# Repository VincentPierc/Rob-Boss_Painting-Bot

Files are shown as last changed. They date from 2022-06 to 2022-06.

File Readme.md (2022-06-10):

# Rob Boss - Painting Robot (Disciple of Bob Ross)
#### Contributors: Vincent Pierce, Conrad Kinsey, Hayden Jeanor

## Contents

- [Overveiw](https://github.com/VincentPierc/Rob-Boss_Painting-Bot#overview)
- [Mechanical Design](https://github.com/VincentPierc/Rob-Boss_Painting-Bot#mechanical-design)
    - [Design Process](https://github.com/VincentPierc/Rob-Boss_Painting-Bot#design-process)
        - [First Iteration](https://github.com/VincentPierc/Rob-Boss_Painting-Bot#first-iteration)
        - [Redesign](https://github.com/VincentPierc/Rob-Boss_Painting-Bot#redesign)
    - [Final Implementation](https://github.com/VincentPierc/Rob-Boss_Painting-Bot#final-implementation)
        - [Paintbrush Actuation](https://github.com/VincentPierc/Rob-Boss_Painting-Bot#paintbrush-actuation)
        - [Matching the 2D Kinematics](https://github.com/VincentPierc/Rob-Boss_Painting-Bot#matching-the-2d-kinematics)
        - [Main Housing](https://github.com/VincentPierc/Rob-Boss_Painting-Bot#main-housing)
    - [Key Takeaways](https://github.com/VincentPierc/Rob-Boss_Painting-Bot#key-takeaways)
        - [Gear Reduction](https://github.com/VincentPierc/Rob-Boss_Painting-Bot#gear-reduction)
        - [Don’t Reinvent the Wheel](https://github.com/VincentPierc/Rob-Boss_Painting-Bot#dont-reinvent-the-wheel)
        - [Add a Third Dimension](https://github.com/VincentPierc/Rob-Boss_Painting-Bot#add-a-third-dimension)
- [Electrical Design](https://github.com/VincentPierc/Rob-Boss_Painting-Bot#electrical-design)
    - [Motor Controlling](https://github.com/VincentPierc/Rob-Boss_Painting-Bot#motor-controlling)
    - [Solenoid Actuating](https://github.com/VincentPierc/Rob-Boss_Painting-Bot#solenoid-actuating)
- [Software Design](https://github.com/VincentPierc/Rob-Boss_Painting-Bot#software-architecture)
    - [Software Architecture](https://github.com/VincentPierc/Rob-Boss_Painting-Bot#software-architecture)
        - [Draw Wrapper](https://github.com/VincentPierc/Rob-Boss_Painting-Bot#draw-wrapper)
        - [Find Thetas](https://github.com/VincentPierc/Rob-Boss_Painting-Bot#find-thetas)
     - [Computer Code](https://github.com/VincentPierc/Rob-Boss_Painting-Bot#computer-code)
        - [Live Plotting](https://github.com/VincentPierc/Rob-Boss_Painting-Bot#live-plotting)
        - [Gif Generation](https://github.com/VincentPierc/Rob-Boss_Painting-Bot#gif-generation)
        - [Theta Timeline](https://github.com/VincentPierc/Rob-Boss_Painting-Bot#theta-timeline)
    - [Kinematics](https://github.com/VincentPierc/Rob-Boss_Painting-Bot#kinematics)
        - [Newton Raphson](https://github.com/VincentPierc/Rob-Boss_Painting-Bot#newton-raphson)

## Overview
Rob Boss (disciple of Bob Ross) is a 2 1/2 degree of freedom pen-plotting robot with a twist. This robot is capable of painting whatever HPGL file that is uploaded to its hard-drive. The project was created for our ME 405 Mechatronics term project at California Polytechnic State University San Luis Obispo.

With an STM32 Arm Cortex MCU on a Nucleo-64 board as the brains of the robot, we designed a surrounding electro-mechanical system from scratch to give a 3-dimensional structure to the robot. In combination with the software we designed and uploaded on the STM32, the robot arm can paint any image you can draw on illustrating software. Detailed design parameters can be found in the [Mechanical Design](https://github.com/VincentPierc/Rob-Boss_Painting-Bot#mechanical-design), [Software Design](https://github.com/VincentPierc/Rob-Boss_Painting-Bot#software-design), and [Electrical Design](https://github.com/VincentPierc/Rob-Boss_Painting-Bot#electrical-design) sections.

The completed robot is able to synchronously draw any HPGL image with color, refill when low on paint, and plot the image on a computer. The video below shows Rob Boss’s full capabilities.

Rob Boss - Painting Robot (https://www.youtube.com/watch?v=zsSy63GS3jI)

## Mechanical Design

### Design Process

Considering all group members of the project are electrical engineers, we decided to go with a rather basic mechanical design which ended up being rather complex after multiple iterations. The mechanical design of the robot was largely based upon two parameters:

1. adhere to the [kinematics](https://github.com/VincentPierc/Rob-Boss_Painting-Bot#kinematics) of the program we were implementing
	- this required lighter components to be used towards the end of the arm because of the large amount of leverage being produced by the arm being in air
2. design around the materials we had at our disposal or that we could buy on a college student's budget

#### First Iteration
 Because our design was based on the traditional "arm" configuration with a "shoulder" and "elbow" joint, we would need a stepper motor driving each joint. In the first iteration of the robot, we chose to use one large stepper motor to drive the shoulder joint and one smaller stepper motor to drive the elbow joint. This iteration had the placement of the smaller motor at the location of the elbow joint, so it required the motor to be lighter. This ended up presenting torque problems in the future.

 In order to transfer the motor torque into arm angle movement, simple elbow pieces were created to directly transfer the movement to the arm. The two armatures, main housing, and the motor elbows were designed in solidworks and 3D printed. The first iteration, shown below, failed because the small motor did not produce enough torque to move the small arm.

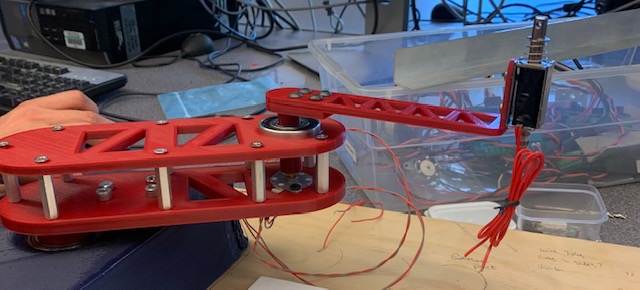
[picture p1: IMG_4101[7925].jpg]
First Iteration


#### Redesign
Upon the realization that we could not use the small motor, we redesigned the large arm to use a large motor to drive the small arm mounted above the large motor already driving the large arm. Placing the small arm motor at the shoulder joint reduced the weight towards the end of the arms. However, it required the use of a driving belt and parametric pullies.

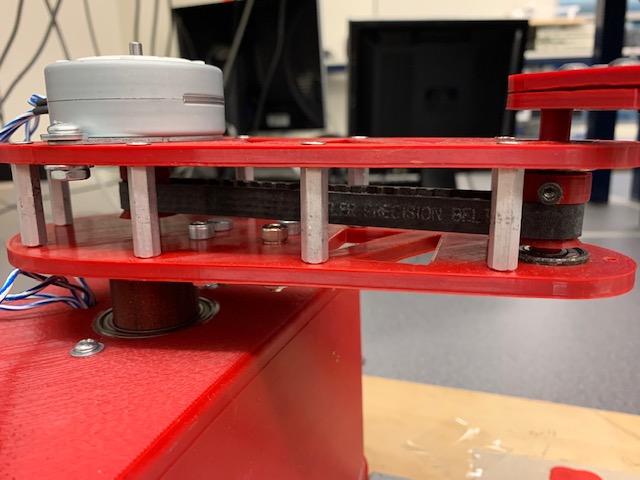
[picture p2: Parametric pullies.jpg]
Parametric Pulley System


Through the guidance of our fellow classmates who are majoring in mechanical engineering, we did not have to design our own parametric pullies. Rather, we pulled [customizable parametric pullies](https://www.thingiverse.com/thing:16627) from [Thingiverse](https://www.thingiverse.com/) and edited them on [OpenSCAD](https://openscad.org/) to meet our mechanical design needs. In order to have variable tensioning of the drive belt, the holes that mount the small arm motor are elongated.

### Final Implementation
The images below show the final form of the robot. Many of the parts of the robot were designed to be fastened together using hardware that was found in the lab. Each of the [parts](https://github.com/VincentPierc/Rob-Boss_Painting-Bot/tree/main/Rob_Boss_Mechanical_Design) were 3D printed and assembled using the fasteners. Another standout design aspect is the reduction of weight in the armatures while maintaining rigidity using triangular cutouts.

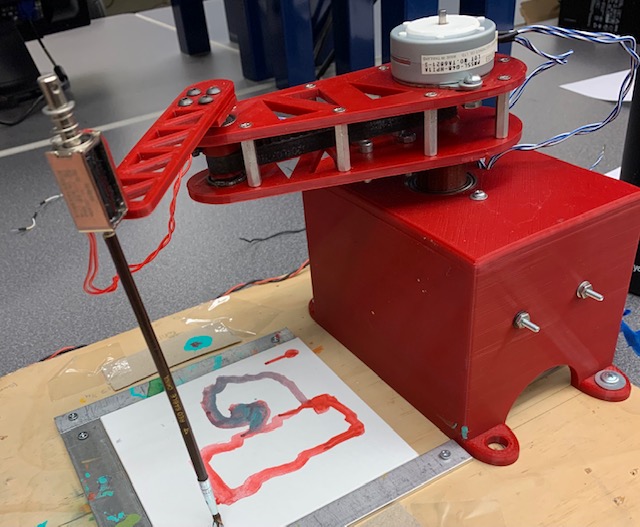
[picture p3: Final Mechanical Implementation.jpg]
Final Mechanical Implementation


#### Paintbrush Actuation
For the half degree of freedom, we chose a lightweight [solenoid actuator](https://www.amazon.com/dp/B07VC5JKYG?psc=1&ref=ppx_yo2ov_dt_b_product_details). This solenoid provides 5N of push/pull force which is plenty to raise and lower a 50 gram paintbrush. The modified paint brush being actuated was threaded into the end of the solenoid plunger.

#### Matching the 2D Kinematics
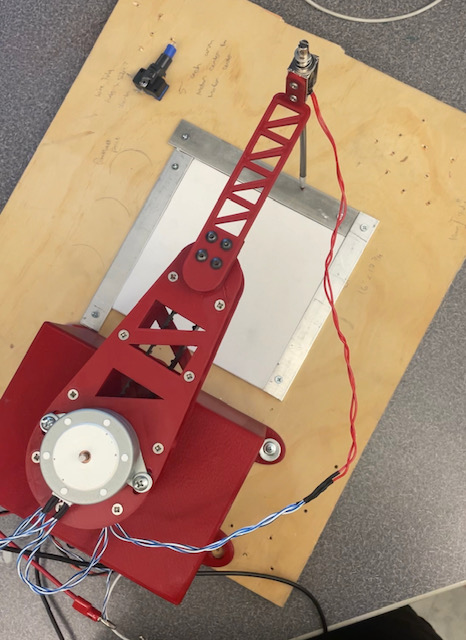
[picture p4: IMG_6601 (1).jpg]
Armature View


Top down view of robot arm used for drawing. Mechanical design implemented a theta-theta rotation about 2 pivot points which, when combined with a solenoid, produced 2 1/2 degrees of freedom. To satisfy the calculated kinematics, both arms were designed so that they would have equivalent lengths from pivot point to pivot point and from pivot point to the center of the paint brush. These lengths were chosen to be 5 inches each because a 10 inch radius covers the desired painting area.

#### Main Housing
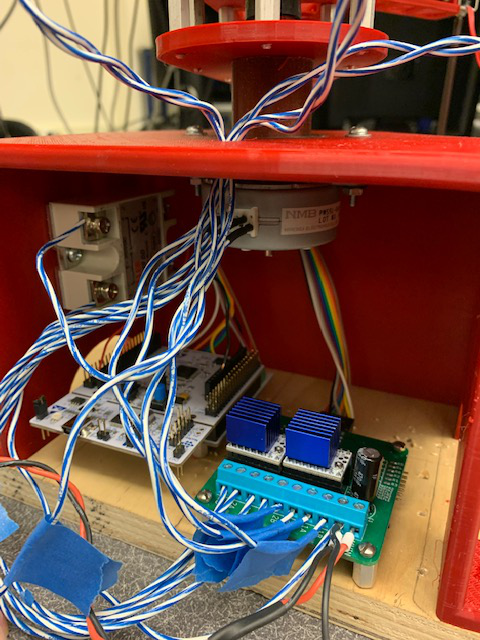
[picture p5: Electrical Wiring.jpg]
Housing View


Side View of robot main housing. The housing was designed so that the arm is ~ 5 inches off canvas it will draw on. Additionally, all electronics (solenoid relay, STM32, Shoe of Brian and breakout board) including their wiring could be securely placed out of reach from the rotating arm.

### Key Takeaways

#### Gear Reduction
Gear reduction from the motor would increase the resolution. The large arm motor ended up having much worse resolution even with microstepping implemented. In hindsight, having the motor drive the arm using another parametric pulley system with gear reduction would have resulted in slower painting speed but much better resolution.

#### Don't Reinvent the Wheel
Starting the project, we originally thought that every aspect of the project had to be original and designed ourselves. In reality, trying to design gears in solidworks is an unnecessary waste of time when someone else on the internet has already done so and published their work for free. Rather, our time is more well spent designing our own innovations.

#### Add a Third Dimension
Originally, both arms were going to be designed using only one dimension. However, the larger arm ended up getting a top which allowed for more stability in the small arm elbow piece that now had two contact points with barings rather than one. The small arm as well as the large arm motor elbow ended up not being so rigid because of the lack of a "3rd dimension."

## Electrical Design
The three actuating devices (motors and solenoid) of the robot are controlled via an electrical system consisting of a central microcontroller, motor-interfacing breakout board, and power system. The overall wiring between the devices are shown below.

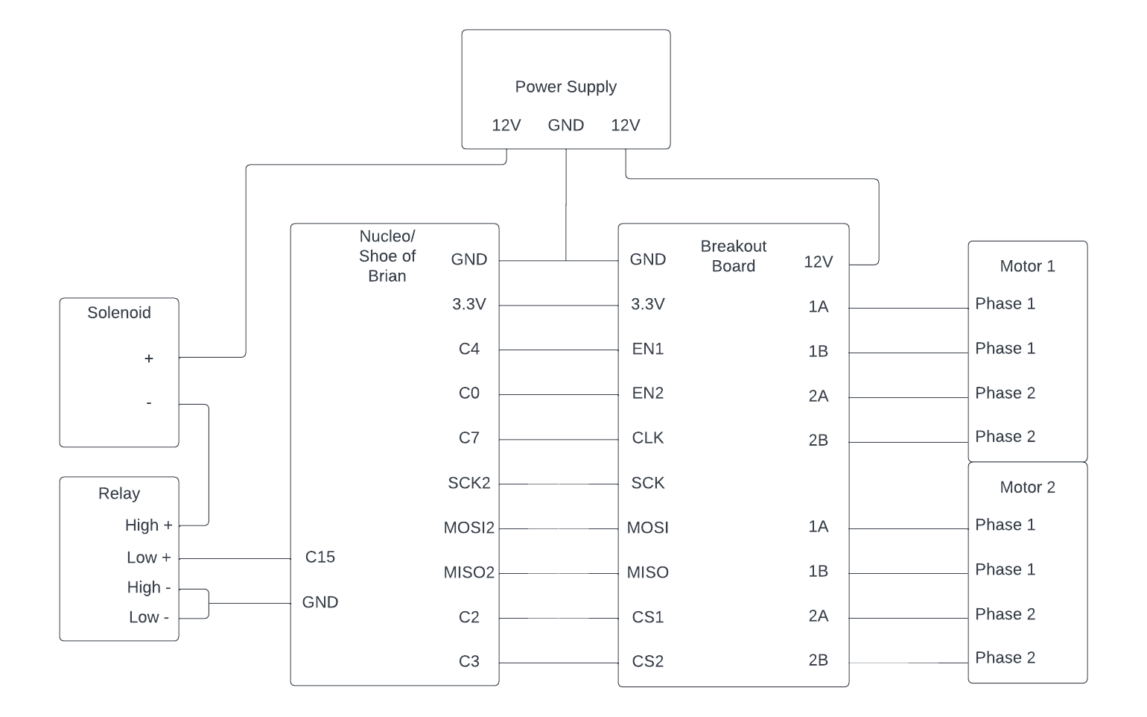
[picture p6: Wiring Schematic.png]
Wiring Diagram


### Motor Controlling
The motors are being controlled by the microcontroller sending position signals via SPI over the bus connected between the MCU and the motor-interfacing breakout board. The breakout board houses a [TMC2208](https://www.mouser.com/datasheet/2/256/TMC220x_TMC2224_datasheet_Rev1_09-1879275.pdf) stepper motor driver and [TMC4210](https://www.mouser.com/datasheet/2/256/TMC4210_Datasheet_Rev_1_05-1878621.pdf) microcontroller-motordriver interface for each motor. To simplify the complexity of these chips, they convert motor position to SPI signals readable by the MCU and vice versa to get real time motor position and send target motor position.

### Solenoid Actuating
 In order to provide the power needed for the solenoid to acutate, a [solid state relay](https://www.amazon.com/SSR-100DD-Solid-State-Relay-Module/dp/B07PFDJQLV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) was used to convert a 3.3V signal from the microcontroller to 12V, 600mA power supply signal.

## Software Design

### Software Architecture
The overarching software architecture uses a cooperative multitasking scheduler. Each of the tasks the robot performs was created with the other tasks in consideration. The robot first parses through the file and creates a list with the first element of which being the instruction name and all subsequent elements being the numbers associated with that instruction. The file then runs through the two processing tasks to interpret the instructions, move the robot, and send the data to the computer.

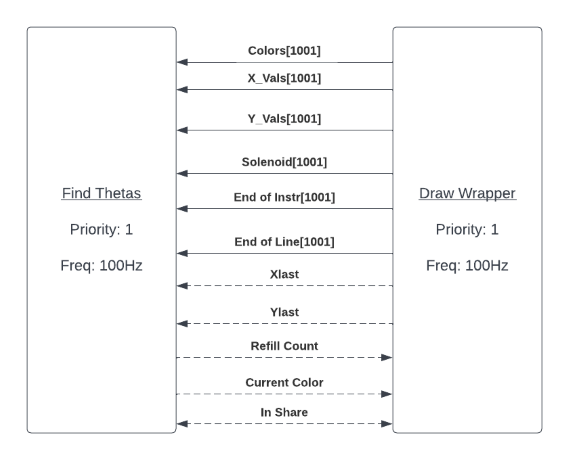
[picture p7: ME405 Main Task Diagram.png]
Main Task Diagram


#### Draw Wrapper
The main task of the assignment is the Draw Wrapper task. The function is named Draw Wrapper because it calls the draw function. The actual purpose of the task is to iterate through the instruction list and process a single instruction each time it is called. It does so through popping the first value of the instruction list then calling the draw function on the popped instruction list. It is inside of the draw function that the instruction is processed. If the instruction is an IN instruction, the function will place the initial point of (0,0) into the X_Vals and Y_Vals queues to set the initial location of the motor when it runs. If an IN instruction is called after this, it will be deemed the end of the list and the motors will reset to their fully extended position. If the instruction is SP, the color selected by the SP instruction will be set as the value for the shared variable curcolor. If a PD or PU function is received, the function will first set the pen value to 1 or 0 with 1 being the pen down state and 0 being the pen up state. The function then runs the interpolation function created in Lab 3. All x and y values are then pushed into the X_Vals and Y_Vals queues. When these values are pushed into the queues, the values of the current color, whether this is the end of instruction and whether this is the end of the file, are also pushed to their respective queues. This task runs with a period of 10ms.

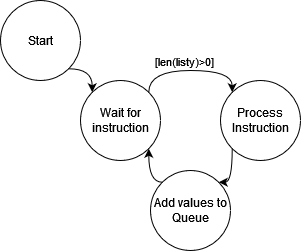
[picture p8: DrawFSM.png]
drawFSM


#### Find Thetas
When the task is first initialized it generates a list of size 2 that will be used for temporary theta storage. To be more memory efficient, this could have been a float array of size 2. However, the difference between an array of size 2 and a list of size 2 was deemed negligible in this case since the list would be reused in each call. After creating the list, the remaining variables represent the initial guesses for the Newton Raphson function and an initial color value of curcolor. The function then checks the size of the X_Vals queue to see if the Draw Wrapper task has been called. If there are values in the queue, they are read and fed into the Newton Raphson function to find the theta values. Once appropriate data values are found, they are converted to between pi and -pi. This is to prevent the robot from spinning in circles after finding a solution a full rotation off from the robot's current position. The theta, solenoid, EOI(End Of Instruction), and EOF (End Of File) bits are then sent over UART to the computer for the live drawing. Once that is done, the motors are then moved to the new theta positions.

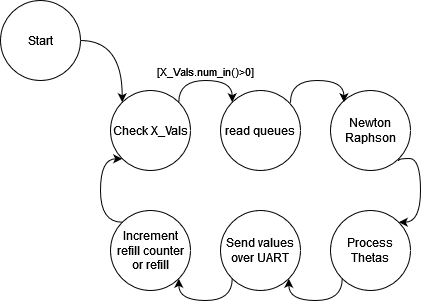
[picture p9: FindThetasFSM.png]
thetaFSM


### Computer Code
For the "Bells and Whistles" of our assignment, we opted to go with a computer software implementation. The code, running simultaneously to the code on the Nucleo, generates various graphs to visualize what Rob is supposed to be doing. As the computer code is all one function named main(), we have split up the portions by generated graphic for ease of reading.

[Code can be found here](https://github.com/VincentPierc/Rob-Boss_Painting-Bot/blob/main/Code/Computer_Code.py)

#### Live Plotting
The live plotting is the first part of the computer code to be run after initializing all necessary variables. The function makes use of a double nested while loop. The first loop waits for the EOF bit and sets the input list to be zeros, while the second waits for the EOI bit and sets the list to the incoming values. Each time these values are read from the UART, a graph is generated with all past points and the current point. The graph also has an updated location of the lines representing the robot's arms, with these arms pointing to the latest point. Lines are only drawn between points in the case of both solenoid bits being set high and are drawn using the color input over UART.

#### Gif Generation
The Gif Generation function runs directly after the Live plotting finishes and mirrors the Live Plotting portion closely. The difference is that it uses a list of the UART and a counter to iterate instead of the two for loops present in the Live Plotting function. The output of this section is an animated gif saved under the name "func.gif".

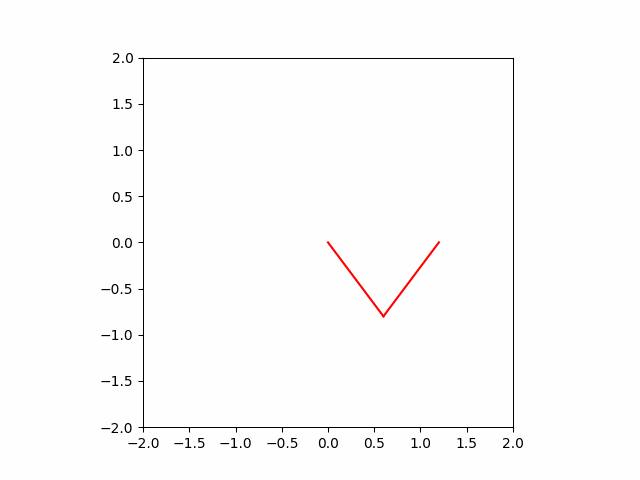
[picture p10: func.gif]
Example


#### Theta Timeline
Once the gif of the plot is generated, a graph showing the values of theta 1 and 2 over the number of UART reads is generated. The graph served to confirm our robot was generating proper values during the testing stages. We left the graphs in as they serve as reassurance that the robot is functioning properly and are a clear indicator the computer code has finished running.

### Kinematics
The requirement of the project is to create a robot that draws with two and a half degrees of freedom not using the traditional cartesian coordinate system. For this project, we implemented a design that has two finite length armatures with variable angles of direction.

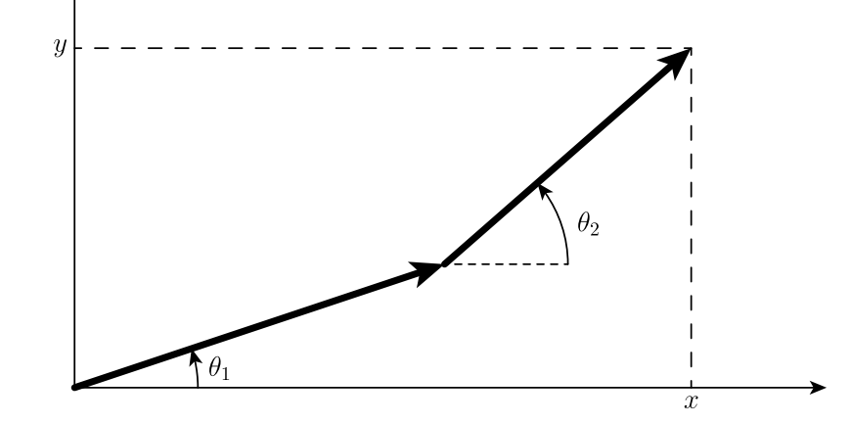
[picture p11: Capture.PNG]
Forward Kinematics


#### Newton Raphson
Even though the robot works in terms of two angles, all the data parsed from the input (HPGL) file is in terms of cartesian coordinates. The heart of Rob's ability to draw lies in the Newton Raphson algorithm which allows us to convert (x, y) coordinates into (theta1, theta2) coordinates. Allowing the robot to draw images like the flower drawn below.

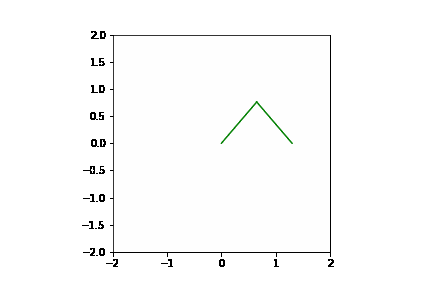
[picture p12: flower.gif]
Animation Drawing


This conversion, or mapping, of coordinate systems is considered kinematics and deals with how driving actuators (motors) affects end-effector coordinates (pen-plotter position). Newton Raphson allows us to iteratively solve for motor coordinates which produce x, y coordinates closer and closer to our target position.

Animated Draw

Above is the computer animation of Rob drawing a cross, below is a link to the video of Rob actually drawing.

Cross Drawing (https://www.youtube.com/shorts/cKq7Di-0tEg)

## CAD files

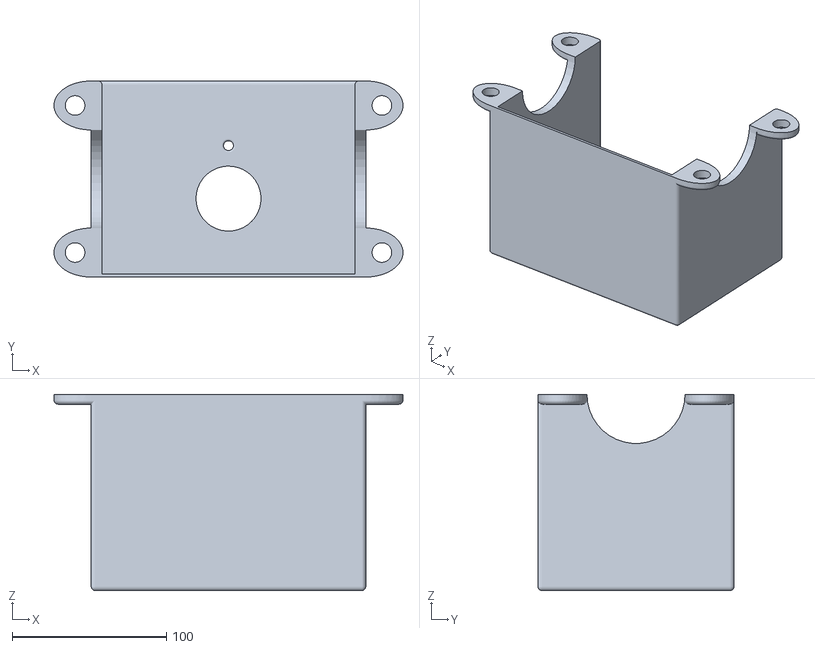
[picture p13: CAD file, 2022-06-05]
Rob_Boss_Mechanical_Design/Main Housing 7in width.STL
226.0 x 127.0 x 127.0

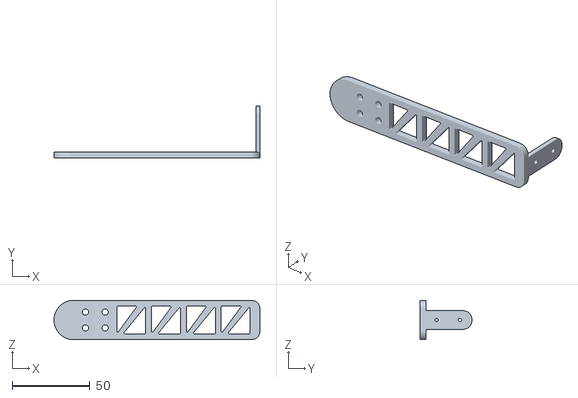
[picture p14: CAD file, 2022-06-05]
Rob_Boss_Mechanical_Design/small arm.STL
132.7 x 33.3 x 25.4

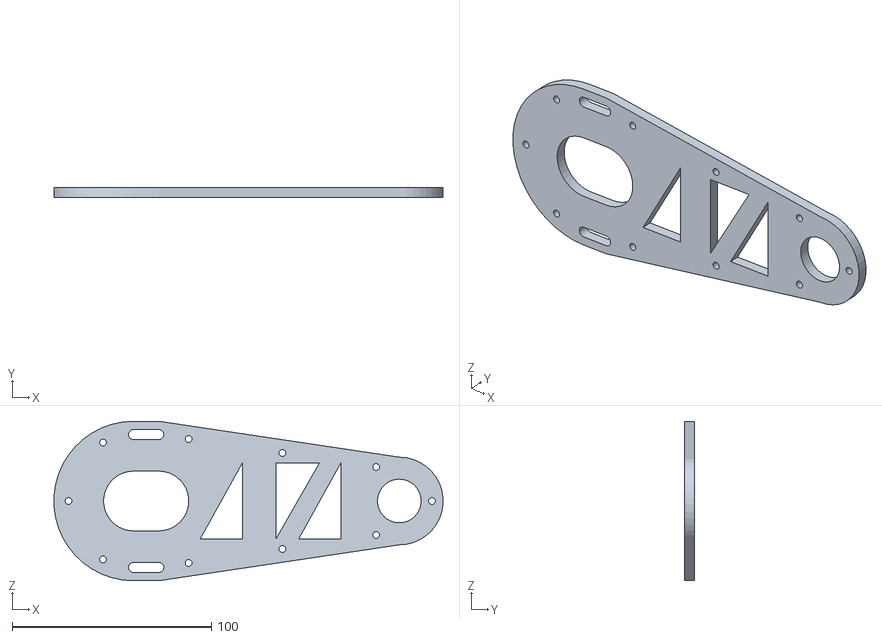
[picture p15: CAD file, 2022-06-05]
Rob_Boss_Mechanical_Design/large arm top 2.0.STL
195.2 x 5.08 x 80.0

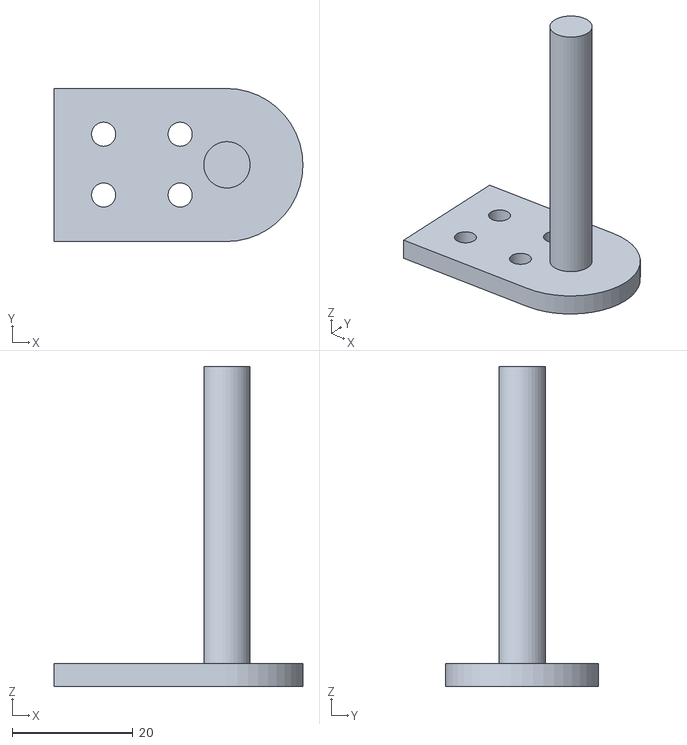
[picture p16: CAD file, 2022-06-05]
Rob_Boss_Mechanical_Design/Small arm elebow 2.0.STL
41.3 x 25.4 x 53.1

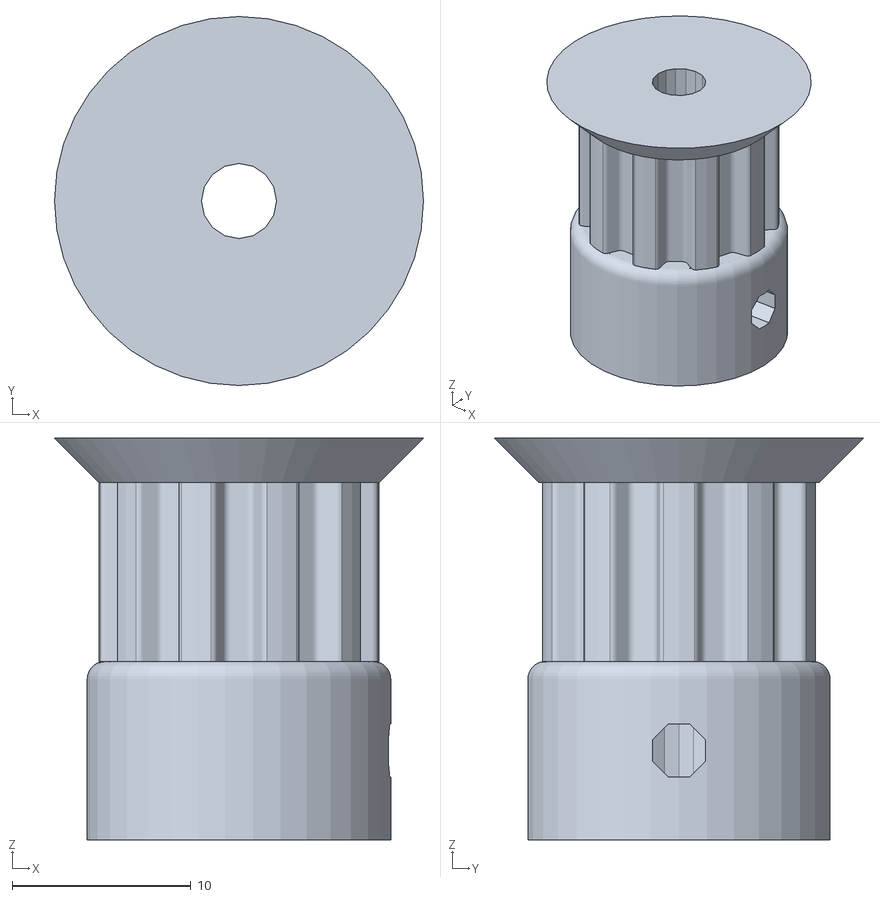
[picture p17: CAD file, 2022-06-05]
Rob_Boss_Mechanical_Design/motor side pully.stl
20.7 x 20.7 x 22.5

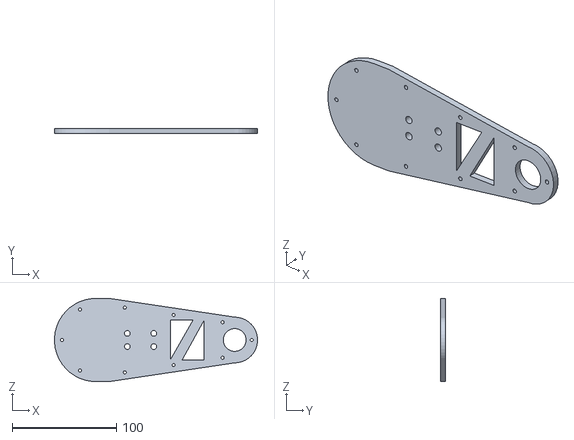
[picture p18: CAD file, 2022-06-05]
Rob_Boss_Mechanical_Design/large arm bottom 2.0.STL
195.2 x 5.08 x 80.0

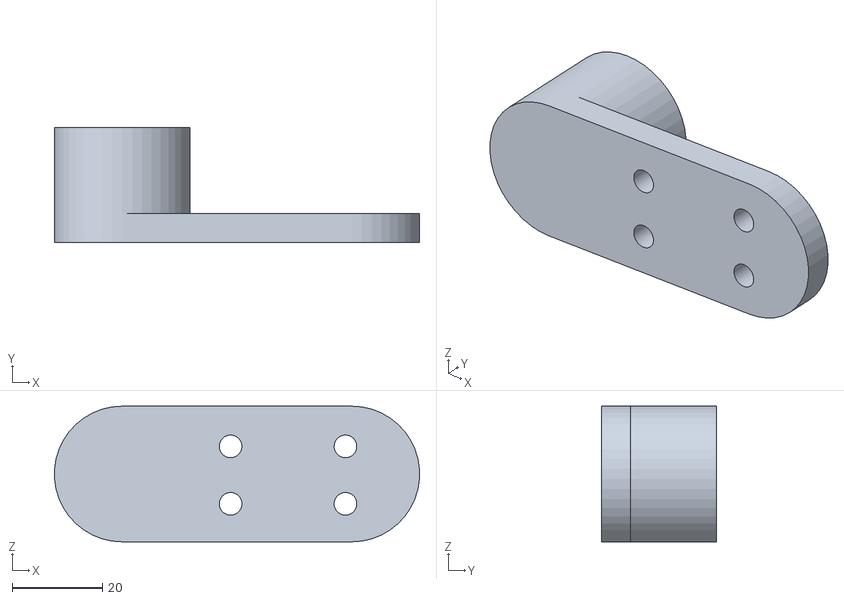
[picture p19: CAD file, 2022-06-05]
Rob_Boss_Mechanical_Design/Large motor elebow.STL
80.7 x 25.3 x 30.0

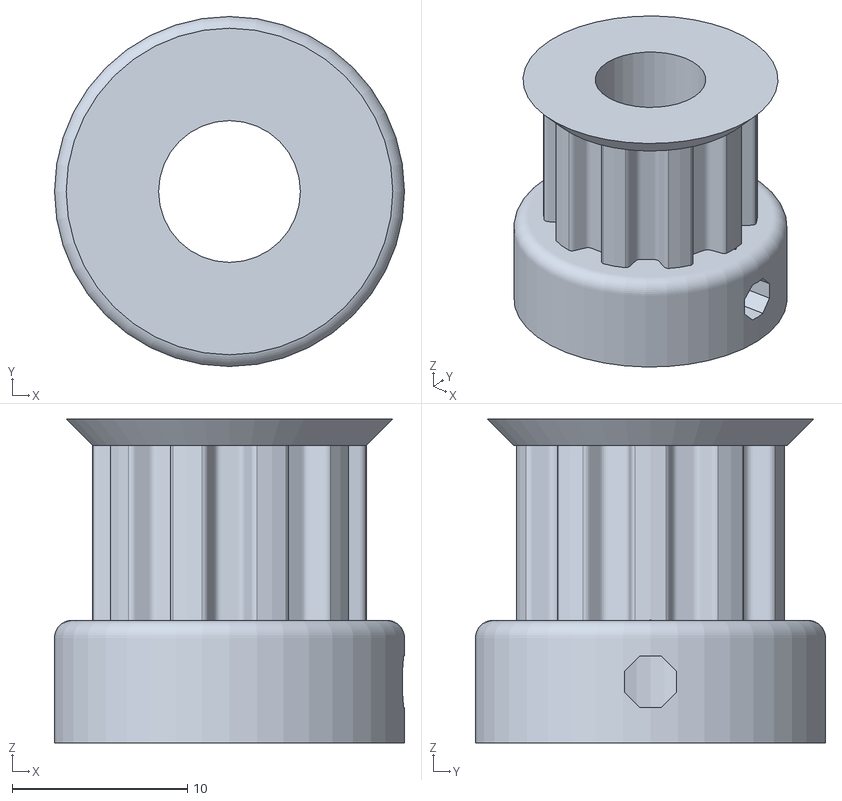
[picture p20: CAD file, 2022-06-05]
Rob_Boss_Mechanical_Design/end of arm pully.stl
20.0 x 20.0 x 18.5

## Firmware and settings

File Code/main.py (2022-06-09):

import pyb, micropython
from pyb import Pin, Timer
from pyb import repl_uart
from ulab import numpy as np
import gc
import pyb
import cotask
import task_share
from stepper import *
from pen import *
import math


class solenoidobj():
    def __init__(self):
        self.drawing = 0

def f(theta):
    return [50*math.cos(theta[0])+50*math.cos(theta[1]) , 50*math.sin(theta[0])+50*math.sin(theta[1])]

def g(x, theta):
    return np.array(x) - np.array(f(theta))

def dg_dtheta(theta):
    return np.array([[50*math.sin(theta[0]), 50*math.sin(theta[1])], [-50*math.cos(theta[0]), -50*math.cos(theta[1])]])

def NewtonRaphson(fcn, jacobian, guess, thresh):
    theta = guess
    while(abs(fcn(theta)[0]) > thresh or abs(fcn(theta)[1]) > thresh):
        theta = theta - np.dot(np.linalg.inv(jacobian(theta)) , fcn(theta))
    return theta

def myraph(dest, guess):
    theta = NewtonRaphson(lambda theta: g(dest,theta), dg_dtheta, guess, 1e-4)
    return theta




def parseHPGL(filename):
    """Takes input hpgl file and outputs double nested list. First list is lines (only 1), second is instructions"""
    im = open(filename, "r")
    lines = im.readline()
    lines = lines.split(";")  #lines[row] becomes another list instead of str
    
    for point in range(len(lines)): #
        lines[point] = lines[point][0:2] + " " + lines[point][2:]
        lines[point] = lines[point].split(',')
        lines[point] = lines[point][0].split(' ') + lines[point][1:]

    return lines

def draw(instr, plotting):
    """Takes instruction in list form ([instruction, points]) from parseHPGL function and fills queue with data """
    interpolated_xy_points = []
    plots = []
    if instr[0] == 'IN':  # IN is ending sequence, first IN must be deleted in HPGL file
        if inshare.get() == 0:
            inshare.put(1)
            xlast.put(0)
            ylast.put(0)
            pass
        else:
            solenoid.put(0)
            X_Vals.put(40)
            Y_Vals.put(0)
            endofinstruction_Vals.put(1)
            endoffile_Vals.put(1)
            colors.put(curcolor.get())
    
    elif instr[0] == 'SP':
        curcolor.put(int(instr[1]))

    elif instr[0] == 'PU':
        plotting.drawing = 0
        interpolated_instr_points = interpolate(instrconv(instr),[xlast.get(), ylast.get()])
        interpolated_xy_points.append(interpolated_instr_points) # converting instruction into points and interpolation of that data
        for i in range(len(interpolated_instr_points)-1):
            solenoid.put(plotting.drawing)
            X_Vals.put(interpolated_instr_points[i][0])
            Y_Vals.put(interpolated_instr_points[i][1])
            colors.put(curcolor.get())
            endofinstruction_Vals.put(0)
            endoffile_Vals.put(0)
        solenoid.put(plotting.drawing)
        X_Vals.put(interpolated_instr_points[-1][0])
        Y_Vals.put(interpolated_instr_points[-1][1])
        colors.put(curcolor.get())
        endofinstruction_Vals.put(1)
        endoffile_Vals.put(0)
        xlast.put(interpolated_instr_points[-1][0])
        ylast.put(interpolated_instr_points[-1][1])

        #x_actuals = [[x[0]/2/math.pi*384,(x[1]+x[0])/2/math.pi*384] for x in interpolated_thetas]

        # funtion to raise solenoid
        # loop to move through target locations

    elif instr[0] == 'PD':
        plotting.drawing = 1
        interpolated_instr_points = interpolate(instrconv(instr),[xlast.get(), ylast.get()])
        interpolated_xy_points.append(interpolated_instr_points) # converting instruction into points and interpolation of that data
        for i in range(len(interpolated_instr_points)-1):
            solenoid.put(plotting.drawing)
            X_Vals.put(interpolated_instr_points[i][0])
            Y_Vals.put(interpolated_instr_points[i][1])
            colors.put(curcolor.get())
            endofinstruction_Vals.put(0)
            endoffile_Vals.put(0)
        solenoid.put(plotting.drawing)
        X_Vals.put(interpolated_instr_points[-1][0])
        Y_Vals.put(interpolated_instr_points[-1][1])
        colors.put(curcolor.get())
        endofinstruction_Vals.put(1)
        endoffile_Vals.put(0)
        xlast.put(interpolated_instr_points[-1][0])
        ylast.put(interpolated_instr_points[-1][1])

        #x_actuals = [[x[0]/2/math.pi*384,(x[1]+x[0])/2/math.pi*384] for x in interpolated_thetas]

        #interpolate()
        # funcion to drop solenoid
        # loop to move through target locations
        
    #return interpolated_xy_points

def instrconv(instr):
    """Takes Output of interpolate function as input and outputs corresponding x,y coord for interpolation func. """
    instr = instr[1:]  # cuts off "PU" & "PD"
    i = 0
    target = [0]*2
    motor_in = []
    if instr[0] == '':
        return [[0,0]]
    while(i < len(instr)):
        target[0] = int(instr[i])
        target[1] = int(instr[i+1])
        motor_in.append([target[0], target[1]])
        i += 2
    return motor_in

def interpolate(targets, curr_location, resolution = 1):  # too many points for memory right now
    """takes a list of targets [[x,y], ...] and current location and returns a new list 
    with as many points to 
    match the desired resolution. Resolution is in dots per inch(dpi)."""
    if len(curr_location) != 2:  # curr_location must be [x,y] 
        print("not a valid current location")
        return None
    interpolated_list = []
    targets.insert(0, [curr_location[0], curr_location[1]])
    for i in range(len(targets)-1):  # want to interpolate between all items in list
        interpolated_list.append(targets[i])  # always add current target
        x_old, y_old = targets[i][0], targets[i][1]
        x_new, y_new = targets[i+1][0], targets[i+1][1]
        distance_x = x_new - x_old
        distance_y = y_new - y_old
        hyp = math.sqrt(distance_x**2 + distance_y**2)
        num_steps = hyp*resolution
        if num_steps == 0:
            curr_location = [x_new, y_new]
            interpolated_list.append([curr_location[0], curr_location[1]])
        else:
            delta_x = distance_x/(num_steps)
            delta_y = distance_y/(num_steps)
            increment = float(1) / resolution  # increment defines how much our motor should move per point after interpolating
            for i in range(int(num_steps-1)):
                    curr_location[0] = curr_location[0] + delta_x
                    curr_location[1] = curr_location[1] + delta_y
                    interpolated_list.append([curr_location[0], curr_location[1]])
            curr_location = [x_new, y_new]
    interpolated_list.append([targets[-1][0],targets[-1][1]])
    return interpolated_list

def pcalc(a_max, ramp_div, pulse_div):  ## is this a motor1.pcalc func now??
    for pmul in range(128,256,1):
        for j in range(14):
            pdiv = 8*(2**j)
            p = a_max/(128*(2**(ramp_div-pulse_div)))
            pd = pmul/pdiv
            q = pd/p
            if(0.95 < q and 1 > q):
                return pmul, j
    return

def TaskFindThetas():
    theta = []
    lastthet1 = math.pi/4
    lastthet2 = math.pi/6
    col = 2
    while True:
        if X_Vals.num_in() > 0:
            curx = X_Vals.get()+60
            cury = Y_Vals.get()
            theta = myraph([curx,cury], [lastthet1, lastthet2])  # converting target(x,y) -> target(theta1, theta2)
            
            #small arm theta calcs
            if theta[0] > 0:
                theta[0] = theta[0] % (math.pi*2)
                if theta[0] > math.pi:
                    theta[0] = theta[0] - (math.pi*2)
            else:
                theta[0] = theta[0] % (math.pi*2)
                if theta[0] > math.pi:
                    theta[0] = theta[0] - (math.pi*2)

            #small arm theta calcs
            if theta[1] > 0:
                theta[1] = theta[1] % (math.pi*2)
                if theta[1] > math.pi:
                    theta[1] = theta[1] - (math.pi*2)
            else:
                theta[1] = theta[1] % (math.pi*2)
                if theta[1] > math.pi:
                    theta[1] = theta[1] - (math.pi*2)

            lastthet1 = theta[0]
            lastthet2 = theta[1]
            solenoid1 = solenoid.get()
            end_of_instr = endofinstruction_Vals.get()
            end_file = endoffile_Vals.get()
            colold = col
            col = colors.get()
            stuff = ("{:},{:},{:},{:},{:},{:}\r\n".format(theta[0], theta[1], solenoid1, end_of_instr, end_file, col))
            uart.write(stuff)
            if col != colold:
                refill(col)
                refillcount.put(0)
            TaskMoveMotors(theta[0], theta[1], solenoid1, col)
        yield (0)

def TaskMoveMotors(theta1, theta2, solenoid, color):
    """if solenoid:
        actuaute_solenoid(soelnoid)"""
    if solenoid == 1:
        refillcount.put(refillcount.get()+1)
    if refillcount.get() >= 100:
        refill(color)
        refillcount.put(0)
    motor2.setloc(theta1)
    motor1.setloc(theta2-theta1)
    pyb.delay(10)
    PB8.value(solenoid)
    print(solenoid)

    
def drawwrapper():
    while True:
        if len(listy)>0:
            instr = listy.pop(0)
            draw(instr, plotting)
        yield

def refill(color):
    PB8.value(0)
    motor2.setloc(0)
    motor1.setloc(0)
    pyb.delay(2000)
    PB8.value(1)
    pyb.delay(500)
    PB8.value(0)
    pyb.delay(500)
    PB8.value(1)
    pyb.delay(500)
    PB8.value(0)
    pyb.delay(500)
    PB8.value(1)
    pyb.delay(500)
    PB8.value(0)
            
            
    if color == 0:
        [theta1, theta2] = myraph([60,60], [-1*math.pi/4, math.pi/6])
    else:
        [theta1, theta2] = myraph([60,-50], [-1*math.pi/4, 0])

    #small arm theta calcs
    if theta1 > 0:
        theta1 = theta1 % (math.pi*2)
        if theta1 > math.pi:
            theta1 = theta1 - (math.pi*2)
    else:
        theta1 = theta1 % (math.pi*2)
        if theta1 > math.pi:
            theta1 = theta1 - (math.pi*2)

    #Big arm theta calcs
    if theta2 > 0:
        theta2 = theta2 % (math.pi*2)
        if theta2 > math.pi:
            theta2 = theta2 - (math.pi*2)
    else:
        theta2 = theta2 % (math.pi*2)
        if theta2 > math.pi:
            theta2 = theta2 - (math.pi*2)
            
    motor2.setloc(theta1)
    motor1.setloc(theta2-theta1)
    pyb.delay(2000)
    PB8.value(1)
    pyb.delay(500)
    PB8.value(0)
    pyb.delay(500)
    PB8.value(1)
    pyb.delay(500)
    PB8.value(0)
    pyb.delay(500)
    PB8.value(1)
    pyb.delay(500)
    PB8.value(0)

if __name__ == "__main__":

    #initialize clk pin    
    PC7 = Pin(Pin.cpu.C7, mode = Pin.OUT_PP,)  # PC7 configured for GPIO output
    tim = Timer(3, period = 3, prescaler = 0) #timer3 @ 80MHz
    tim.channel(2, pin = PC7, mode = Timer.PWM, pulse_width = 2)
    PB8 = Pin(Pin.cpu.B8, mode = Pin.OUT_PP)  # solenoid pin
    # configures PC7 for PWM modulation to act as a clock signal

    #initialize cs and en pins
    PC2 = Pin(Pin.cpu.C2, mode = Pin.OUT_PP, value = 1)  #CS1
    PC3 = Pin(Pin.cpu.C3, mode = Pin.OUT_PP, value = 1)  #CS2
    PC4 = Pin(Pin.cpu.C4, mode = Pin.OUT_PP, value = 1)  #EN1
    PC0 = Pin(Pin.cpu.C0, mode = Pin.OUT_PP, value = 1)  #EN2
    
    motor1 = stepper(PC2, PC4)
    motor2 = stepper(PC3, PC0)

    # Create a share and a queue to test function and diagnostic printouts
    xlast = task_share.Share('f', thread_protect = False, name = "share 0")
    
    ylast = task_share.Share('f', thread_protect = False, name = "share 1")
    
    inshare = task_share.Share('I', thread_protect = False, name = "share 2")
    
    refillcount = task_share.Share('I', thread_protect = False, name = "share 3")
    
    curcolor = task_share.Share('I', thread_protect = False, name = "share 4")
    
    colors = task_share.Queue ('I', 1000, thread_protect = False, overwrite = False,
                           name = "Colors")

    X_Vals = task_share.Queue ('f', 1000, thread_protect = False, overwrite = False,
                           name = "X Values")

    Y_Vals = task_share.Queue ('f', 1000, thread_protect = False, overwrite = False,
                           name = "Y Values")

    solenoid = task_share.Queue ('i', 1000, thread_protect = False, overwrite = False,
                           name = "sol")
    endofinstruction_Vals = task_share.Queue ('i', 1000, thread_protect = False, overwrite = False,
                           name = "EOI")
    endoffile_Vals = task_share.Queue ('i', 1000, thread_protect = False, overwrite = False,
                           name = "EOF")

    # Create the tasks. If trace is enabled for any task, memory will be
    # allocated for state transition tracing, and the application will run out
    # of memory after a while and quit. Therefore, use tracing only for 
    # debugging and set trace to False when it's not needed
    
    listy = parseHPGL("drawing.hpgl")
    plotting = solenoidobj()
    inshare.put(0)
    
    findthet = cotask.Task (TaskFindThetas, name = 'Task_1', priority = 2, 
                         period = 10, profile = True, trace = False)

    rundraw = cotask.Task (drawwrapper, name = 'Task_2', priority = 2,
                         period = 10, profile = True, trace = False)

    uart = pyb.UART(2, 115200)
    uart.init(115200, bits=8, parity=None, stop = 1)

    listy = parseHPGL("drawing.hpgl")
    plotting = solenoidobj()

    #cotask.task_list.append (taskbut)
    cotask.task_list.append(findthet)
    cotask.task_list.append(rundraw)

    # Run the memory garbage collector to ensure memory is as defragmented as
    # possible before the real-time scheduler is started
    gc.collect ()

    # Run the scheduler with the chosen scheduling algorithm. Quit if any 
    # character is received through the serial port
    vcp = pyb.USB_VCP ()
    while not vcp.any ():
        cotask.task_list.pri_sched()

    # Empty the comm port buffer of the character(s) just pressed
    vcp.read ()
    
    



    

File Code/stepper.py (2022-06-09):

import pyb, micropython
from pyb import Pin, ADC, Timer, ExtInt, SPI
from pyb import repl_uart
import gc
import math
from time import *
import pyb

class stepper():
    def __init__(self, cs, en):
        #this is spiInit
        spi = SPI(2, SPI.CONTROLLER, firstbit = SPI.MSB, baudrate=1000000, polarity=1, phase=1)#SPI latches data on falling edge of clock and CS active low
        # polarity determines idle level for CS, and phase determines whether falling or rising edge of clock latches data from dataline
        self.spi = spi
        self.cs = cs
        self.en = en
        self.en.value(0)
        bits = [0x02, 0x00, 0x00, 0xC0]  # setting X_actual & X_target to same position
        self.writeSPI(bytearray(bits))
        bits = [0x00, 0x00, 0x00, 0xC0]
        self.writeSPI(bytearray(bits))
        
        #write en_sd high
        bits = [0x68, 0x00, 0x00, 0x20]  # MAKE SWITCHES 0 IN IF_CONFIG PG 34
        self.writeSPI(bytearray(bits))

        #write V_MIN
        bits = [0x04, 0x00, 0x00, 0x0f] 
        self.writeSPI(bytearray(bits))
        
        #write V_MAX
        bits = [0x06, 0x00, 0x00, 0xff]  
        self.writeSPI(bytearray(bits))       
        
        #write pulse_div & ramp_div
        bits = [0x18, 0x00, 0xaa, 0x00]  
        self.writeSPI(bytearray(bits))
        
        #calculate pmul & pdiv
        pmul, pdiv = pcalc(1024, 10, 10) # inputs: a_max, pmul, pdiv

        #write pmul & pdiv
        bits = [0b00010010, 0x01, pmul & 0xff, pdiv & 0x0f]    
        self.writeSPI(bytearray(bits))
        
        #write amax
        bits = [0x0c, 0x00, 0x01, 0x00]    
        self.writeSPI(bytearray(bits))
        
        #write ramp_mode
        bits = [0x14, 0x00, 0x00, 0x00]     #set ramp mode #REF_CONF bits see pg 29?????
        self.writeSPI(bytearray(bits))
        

    def readSPI(self, bits):
        self.cs.value(0)
        ba = bytearray(4)
        self.spi.send_recv(bits, ba, timeout = 500)
        self.cs.value(1)
        return ba

    def writeSPI(self,bits):
        self.cs.value(0)
        self.spi.send(bits)
        self.cs.value(1)
        # MOSI line will maintain voltage of last output bit on write bytearray 

    def setloc(self, theta):  # input radians
        where = 192 + int(theta/(2*math.pi)*384)  # 32 bit converted to steps
        bitstar = bytearray([0x00, 0x00, 0xff & (where>>8), 0xff & where])
        self.writeSPI((bitstar))
        ba = bytearray(4)
        bits = bytearray([0x03, 0x00, 0x00, 0x00])
        while [ba[3],ba[2]] != [bitstar[3],bitstar[2]]:
            pyb.delay(10)
            ba = self.readSPI(bits)
#             print("\n Loc")
#             print(ba[3])
            #for idx,byte in enumerate(ba): print(f"b{3-idx}: {byte:#010b} {byte:#04x}")
#             print("\n Target")
#             print(bitstar[3])
            #for idx,byte in enumerate(bitstar): print(f"b{3-idx}: {byte:#010b} {byte:#04x}")


def pcalc(a_max, ramp_div, pulse_div):  ## is this a motor1.pcalc func now?? A: No its not inside the class definition - V
    for pmul in range(128,256,1):
        for j in range(14):
            pdiv = 8*(2**j)
            p = a_max/(128*(2**(ramp_div-pulse_div)))
            pd = pmul/pdiv
            q = pd/p
            if(0.95 < q and 1 > q):
                return pmul, j
    return

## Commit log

2022-06-05 Rename README.md to Landing Page.md
2022-06-05 Rename Landing Page.md to Readme.md
2022-06-09 updated to ensure flower works with new func file
